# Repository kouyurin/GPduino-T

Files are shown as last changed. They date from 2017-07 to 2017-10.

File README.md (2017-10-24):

GPduino-T
=========
## 概要
GPduino-Tは、ESP32搭載のWiFiラジコン戦車制御ボードです。

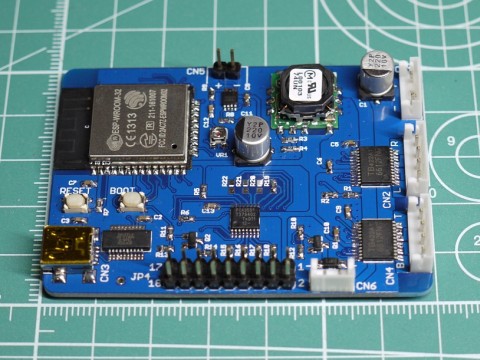
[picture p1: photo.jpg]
写真


以下のことができます。

* DCモータ4個を制御 (最大連続1.2A / 最大瞬間3.0A)
* LED 8個を制御
* サウンド出力
* 赤外線信号(38kHz変調)の送受信
* 電源 3.6V～7.2V (4.8～6V推奨)、電源電圧を監視
* WiFiによる通信　(APにもSTAにもなれる)

また、Waltersons製 1/24 バトルタンクシリーズ互換のIRバトルが可能なファームウェアを提供します。

## ファイル一覧

* hard/GPduino-T/
	* GPduino-T.sch/brd: 回路/基板設計データ(Eagle形式)
	* GPduino-T.pdf: 回路図(PDF)
	* GPduino-T_BOM.xlsx: BOMリスト(Excel形式)
	* GPduino-T.GBL/GBO/GBP/GBS/GML/GTL/GTO/GTP/GTS/TXT: ガーバデータ
* firm/GPduinoT/
	* GPduinoT.ino: ラジコン戦車のArduinoスケッチ
	* *.h, *.cpp: ラジコン戦車のための各種クラス宣言と実装 
* data/
	* cannon.bin: 砲撃音のサウンドデータ
* LICENSE: Apache Licence 2.0です。
	* ただし、回路/基板設計は、Creative Commons Attribution Share-Alike 3.0です。
* README.md これ

## Arduino開発環境のセットアップ
GPduino-T はESP32を搭載しており、Arduino IDEでファームウェアを開発できます。

ここでは、Windows10での開発環境のセットアップについて説明します。他のプラットフォームでも同様です。適宜読み替えてください。

* まず、ArduinoIDE をインストールしておきます。 (ここでは 1.8.2 を使用)
* 残念ながら、Arduino Core for the ESP32はArduino IDEのボードマネージャには対応しておらず、以下のように手作業でインストールする必要があります。
* まず、以下のリポジトリからクローンします。もしもGitが使えない場合、こちらからDownload ZIPして解凍してもかまいません。アップデートの時の手間だけの問題かと思います。
	* ソース: https://github.com/espressif/arduino-esp32.git
    * 保存先: C:/Users/ユーザ名/Documents/Arduino/hardware/espressif/esp32
* 次に、下記のバイナリを実行します。
	* C:/Users/ユーザ名/Documents/Arduino/hardware/espressif/esp32/tools/get.exe
* DOS窓が開いてインストールが実行されます。あとはDOS窓が閉じるまで待ちます。
* ノートン先生をはじめ一部のセキュリティソフトは、いくつかのバイナリをウィルスとして検出してしまうようです。(ノートン先生ではTrojan.Gen.8!cloudとして検出されます。)
* Arduino IDEの[ツール] > [マイコンボード]で[ESP32 Dev Module]を選択します。
* [ツール] > [Upload Speed]で[115200]を選択します。

## Arduinoスケッチ (Waltersonsバトルタンク互換)

Waltersons製 1/24 バトルタンクシリーズ互換の赤外線バトルが可能な以下のファームウェアを提供しています。
* firm/GPduinoT/
	* GPduinoT.ino: ラジコン戦車のArduinoスケッチ
	* *.h, *.cpp: ラジコン戦車のための各種クラス宣言と実装

Waltersonsのバトルタンクの制御基板と置き換える場合には、[こちら](http://d.hatena.ne.jp/licheng/20170421/p1)の結線表を参照してください。

## Arduinoスケッチ (ユーザー独自)
ユーザーが独自にファームウェアを作成する場合は、上記のスケッチを参考にしてください。

ラジコン戦車のための各種クラスを利用するためには、Wire.h と GPduinoR.h をインクルードします。
``` c
#include <Wire.h>
#include "GPduinoR.h"
```
すると、以下のクラスが使用できます。詳細はソースを参照してください。

* Battery: バッテリー電圧の取得
* DcMotor: DCモータの制御
* IR: 赤外線信号の送受信
* Led: LEDの制御
* Solenoid: ソレノイドの制御
* Sound: サウンドの出力
* UdpComm: WiFiによるUDP/IP通信

## Arduinoスケッチの書き込み
* GPduino-TをUSBケーブルでPCに接続します。
* 書き込み時もUSBからの給電は受けません。CN1から給電してください。
* Windows 7以降であればドライバが自動でインストールされ、COMポートとして認識されます。
	* 自動でデバイスが認識されない環境ではFTDIのデバイスドライバをインストールしてください。
* [ツール] > [シリアルポート]でESP32のポートを選択する。
* BOOTボタン(SW2)を押し下げた状態で、RESETボタン(SW1)を押して離します。これで書き込みモードになります。
* Uploadボタンで、ファームウェアを書き込みます。

## サウンドデータの書き込み
Arduinoスケッチとは別にサウンドデータもESP32のフラッシュメモリに書き込みます。

GPduinoT.ino は、フラッシュメモリの0x100000番地から61440バイトの領域に砲撃音のサウンドデータ (data/cannon.bin) が格納されているものとしています。

書き込みツール esptool.exe のあるディレクトリにパスを通しておきます。Windows10なら通常は下記ディレクトリになります。
```
C:\Users\ユーザ名\Documents\Arduino\hardware\espressif\esp32\tools
```
ESP32のBOOTボタン(SW2)を押し下げた状態で、RESETボタン(SW1)を押して離して書き込みモードにします。シリアルポートをPCに接続し、PCでCOMポート番号を確認します。ここではCOM3であったとします。そこで下記のコマンドを実行します。

```
esptool.exe -c esp32 -p COM3 -b 115200 write_flash 0x100000 cannon.bin
```

このサウンドデータは、下記のフォーマットのWAV形式ファイルから、先頭44バイトのヘッダを削除し、さらに符号なし16ビット値形式に変換するために各サンプル値に+0x8000したものです。
* サンプリング周波数 11.025kHz
* 符号つき16ビット量子化
* モノラル

## 既知の問題点

* ~~7.2V電源使用時に発熱が大きい。(3端子レギュレータをDCDCコンバータに置き換えるべき)~~ → rev.2で対応
* ~~サウンドのボリューム調整のためのトリマを追加すべき。~~ → rev.2で対応
* サウンド再生時にCPUがクラッシュする場合があるため、クラッシュ回避のごまかし処理を入れている。
* 無音時にアンプからプツプツ音が出る。
* ブリッジしやすいバターン要修正。 (SOP部品)
* D級アンプのランドパターンが短く、ハンダづけしづらい。

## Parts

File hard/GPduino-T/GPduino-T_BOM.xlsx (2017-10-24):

Gpduino-T BOM
No | Reference | Part Number | Vender | Description | DNP | Qty | Unit Price | Price | Lot Size | Supplier | Supplier Code
1 | C1,4 | 220u10V | NICHICON | チップアルミ電解コンデンサ ニチコンWT |  | 2 | 10 | 20 | 1 | 秋月 | P-10419
2 | C2,3,5-10,13 | 0.1u(1608) | (generic) | 1608型 |  | 9 | 0.325 | 2.925 | 4000 | 秋月 | P-01299
3 | C11,12 | 10nF(1608) | (generic) | 1608型 |  | 2 | 1 | 2 | 100 | 秋月 | P-04660
4 | CN1 | B3B-EH | JST | EH 3極 I型ポスト | DNP | 0 | 21 | 0 | 1 | 共立 | -
5 | CN2 | MUSB-5B-NE-S175 | Useconn Electronics | USBコネクタ Mini B メス |  | 1 | 50 | 50 | 2 | 秋月 | C-05843
6 | CN3,4 | B4B-EH | JST | EH 4極 I型ポスト | DNP | 0 | 21 | 0 | 1 | 共立 | -
7 | CN5,6 | B2B-EH | JST | EH 2極 I型ポスト | DNP | 0 | 16 | 0 | 1 | 共立 | -
8 | CN7 | - | (generic) | 2.54mmピッチ 9ピン×2列 L字ピンヘッダ | DNP | 0 | 77 | 0 | 4 | 共立 | -
9 | D1 | SS2040FL | PANJIT | ショットキーバリアダイオード 40V2A |  | 1 | 15 | 15 | 20 | 秋月 | I-02073
10 | Q1,2 | IRLML8244 | International Rectifier | Nch MOSFET (SOT23パッケージ) |  | 1 | 13 | 13 | 10 | 秋月 | I-06051
11 | R1 | 20k(1608) | (generic) | 1608型 |  | 1 | 0.2 | 0.2 | 2500 | 秋月 | R-06203
12 | R2,5-7,12,13 | 10k(1608) | (generic) | 1608型 |  | 6 | 0.2 | 1.2 | 2500 | 秋月 | R-06103
13 | R3 | 1.5k(1608) | (generic) | 1608型、±0.1% |  | 1 | 57.6 | 57.6 | 5 | RS | 566-872
14 | R4 | 680(1608) | (generic) | 1608型、±0.1% |  | 1 | 57.6 | 57.6 | 5 | RS | 566-361
15 | R8,9 | 150(1608) | (generic) | 1608型 |  | 2 | 0.2 | 0.4 | 2500 | 秋月 | R-06151
16 | R10,11,14-19 | 100(1608) | (generic) | 1608型 |  | 8 | 0.2 | 1.6 | 2500 | 秋月 | R-06101
17 | R20-22 | 100(1608) | (generic) | 1608型 | DNP | 0 | 0.2 | 0 | 2500 | 秋月 | R-06101
18 | SW1,2 | SKRPACE010 | ALPS | 表面実装タクトスイッチ |  | 2 | 20 | 40 | 5 | 秋月 | P-06185
19 | U1 | OKL-T/3-W12N | Murata | DCDCコンバータ |  | 1 | 400 | 400 | 1 | 秋月 | M-06206
20 | U2,5 | TB6621FNG | Toshiba | Dual DCモータドライバ |  | 2 | 306 | 612 | 1 | RS | 770-3797
21 | U3 | FT231XS | FTDI | USBシリアル変換 |  | 1 | 210 | 210 | 1 | 秋月 | I-06713
22 | U4 | ESP-WROOM-32 | Espressif Systems | ESP32 WiFiマイコン |  | 1 | 700 | 700 | 1 | 秋月 | M-11647
23 | U6 | PAM8303 CBSC | DiodesZetex | オーディオD級アンプ |  | 1 | 32.6 | 32.6 | 10 | RS | 790-2966
24 | U7 | PCA9551 PW | NXP | 8チャンネルLEDドライバ |  | 1 | 111 | 111 | 5 | RS | 510-730
25 | VR1 | EVM3YSX50B14 | Panasonic | 半固定抵抗器 10kΩ, 0.15W |  | 1 | 54.2 | 54.2 | 5 | RS | 731-2883
26 | - | - | Elecrow | 基板 |  | 1 | 275.1 | 275.1 | 10 | Elecrow | -
 |  |  |  |  |  |  | Total | 2656.425

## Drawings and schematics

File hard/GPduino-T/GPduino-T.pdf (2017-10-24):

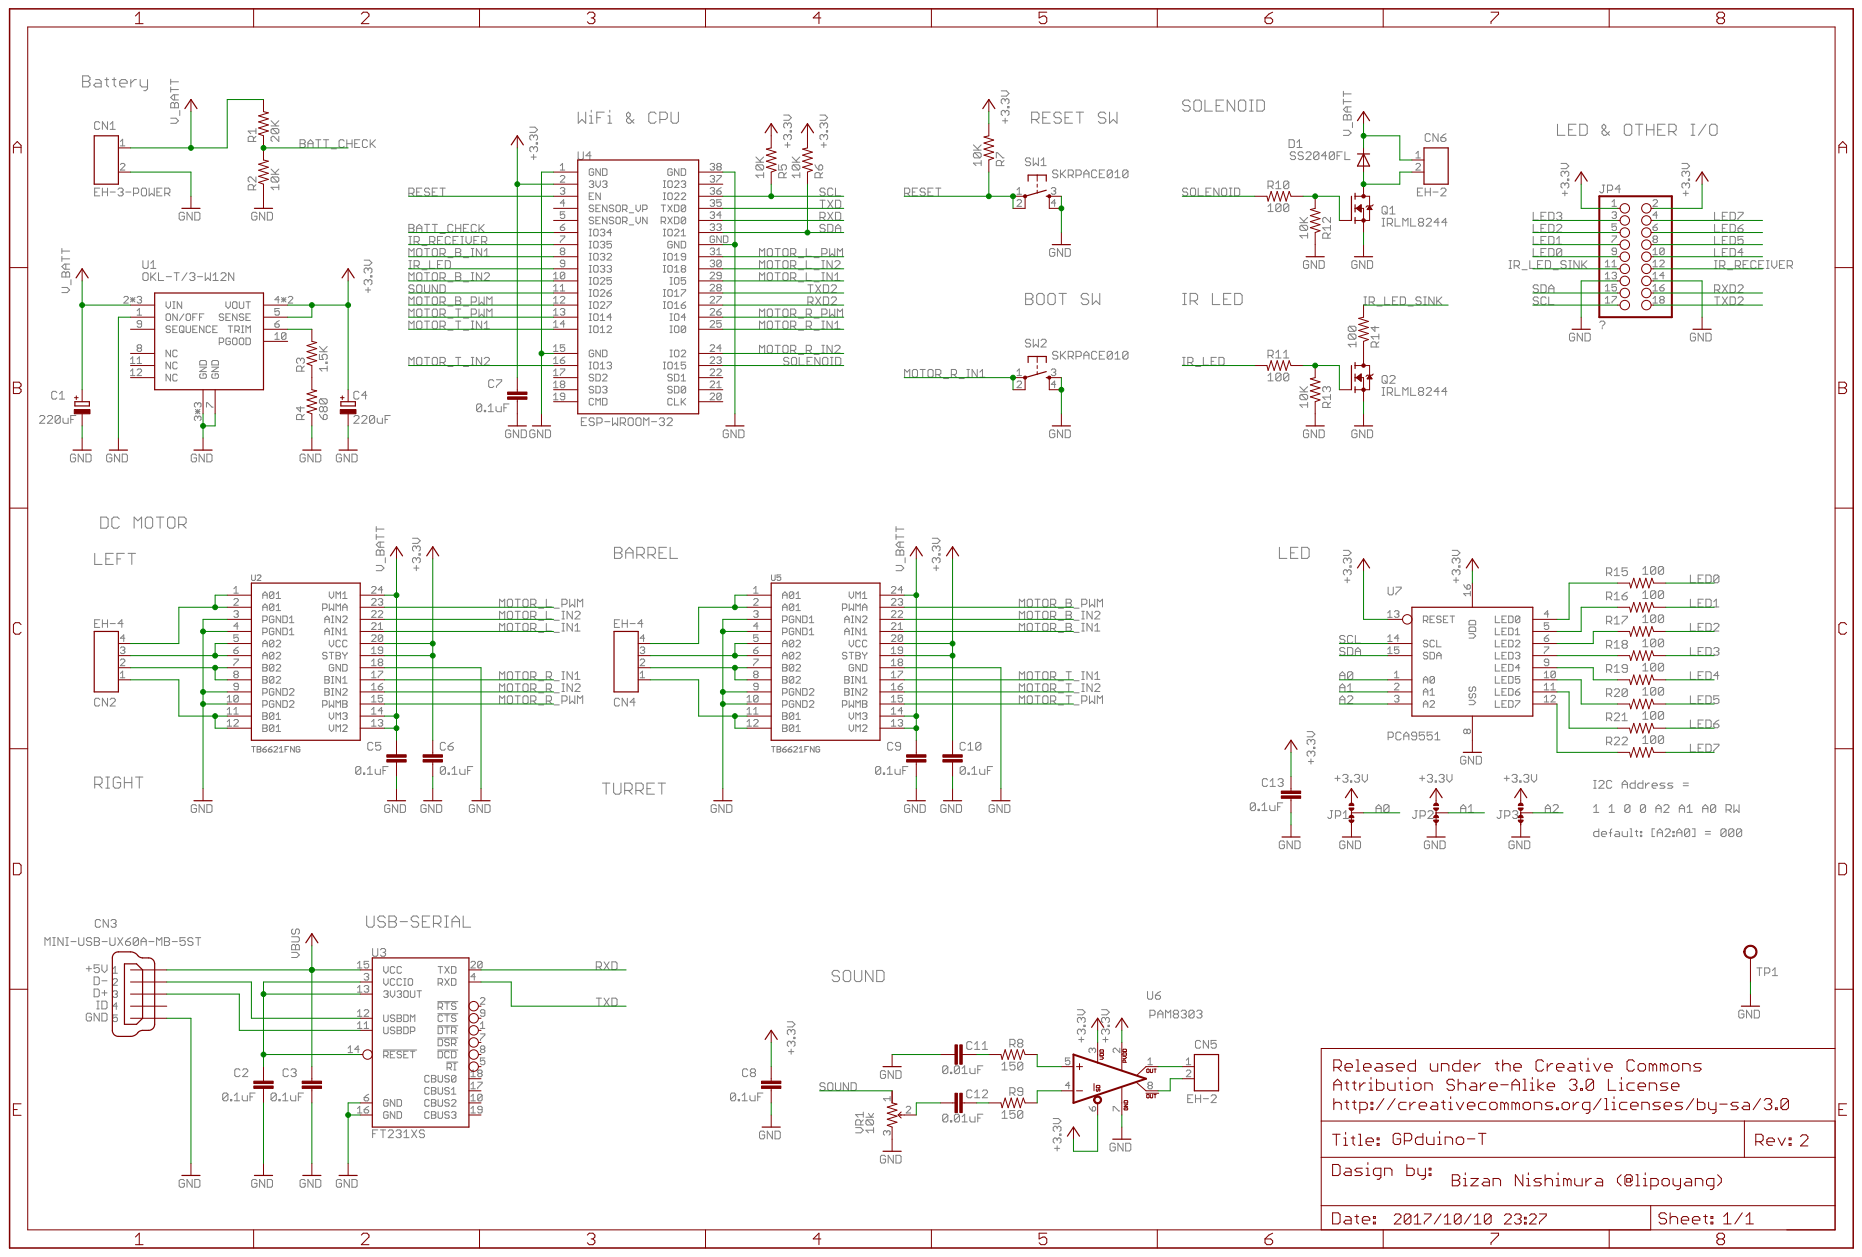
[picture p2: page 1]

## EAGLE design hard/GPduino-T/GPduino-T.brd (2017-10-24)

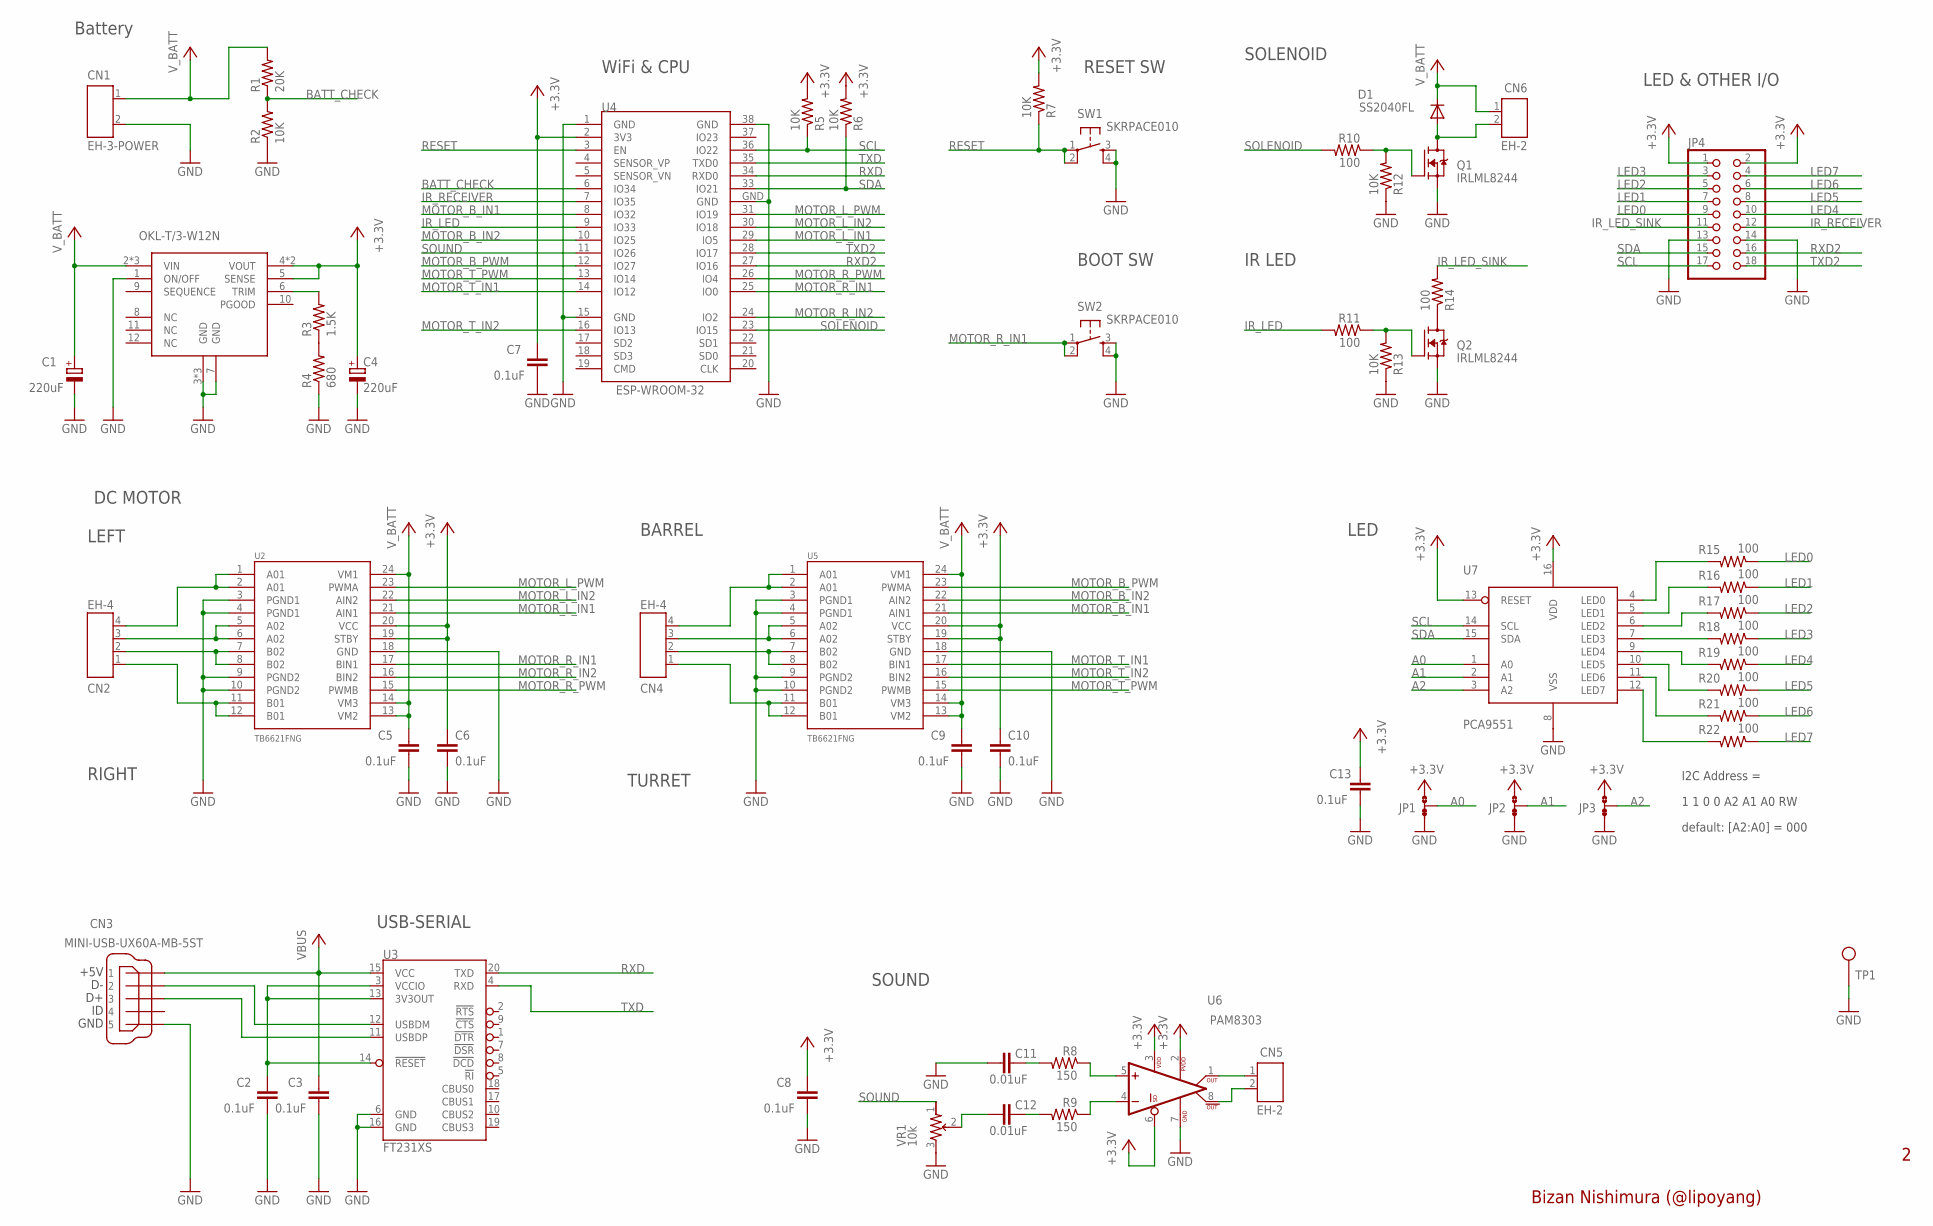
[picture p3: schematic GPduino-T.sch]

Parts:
C1, C4: 220uF; UD-6,3X7,7_NICHICON
C2, C3, C5, C6, C7, C8, C9, C10, C13: 0.1uF; C1608
C11, C12: 0.01uF; C1608
CN1: EH-3-POWER
CN2, CN4: EH-4
CN3: MINI-USB-UX60A-MB-5ST; UX60A-MB-5ST
CN5, CN6: EH-2
D1: SS2040FL; SOD123
JP1, JP2, JP3: JUMP-SHORTB; JUMP-SHORT
JP4: 2X09
Q1, Q2: IRLML8244; SOT23
R1: 20K; 0603-RES
R2, R5, R6, R7, R12, R13: 10K; 0603-RES
R3: 1.5K; 0603-RES
R4: 680; 0603-RES
R8, R9: 150; 0603-RES
R10, R11, R14, R15, R16, R17, R18, R19, R20, R21, R22: 100; 0603-RES
SW1, SW2: SKRPACE010
TP1: TEST_PIN
U1: OKL-T/3-W12N; OKL-T/X-WXXN
U2, U5: TB6621FNG; SSOP24
U3: FT231XS; SSOP20
U4: ESP-WROOM-32
U6: PAM8303; MSOP8
U7: PCA9551; TSSOP16
VR1: 10k; EVM3Y

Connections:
+3V3: C4.+, C6.1, C7.1, C8.1, C10.1, C13.1, JP1.1, JP2.1, JP3.1, JP4.1, JP4.2, R5.2, R6.2, R7.2, U1.4 (VOUT), U1.4@1 (VOUT), U1.5 (SENSE), U2.19 (STBY), U2.20 (VCC), U4.2 (3V3), U5.19 (STBY), U5.20 (VCC), U6.2 (PVDD), U6.3 (VDD), U6.6 (SD), U7.13 (RESET), U7.16 (VDD)
A0: JP1.2, U7.1 (A0)
A01: CN2.4, U2.1 (A01), U2.2 (A01)
A1: JP2.2, U7.2 (A1)
A02: CN2.3, U2.5 (A02), U2.6 (A02)
A2: JP3.2, U7.3 (A2)
A06: CN4.4, U5.1 (A01), U5.2 (A01)
A07: CN4.3, U5.5 (A02), U5.6 (A02)
BATT_CHECK: R1.1, R2.2, U4.6 (IO34)
GND: C1.-, C2.2, C3.2, C4.-, C5.2, C6.2, C7.2, C8.2, C9.2, C10.2, C11.2, C13.2, CN1.2, CN3.5, JP1.3, JP2.3, JP3.3, JP4.13, JP4.14, Q1.2 (S), Q2.2 (S), R2.1, R4.1, R12.1, R13.1, SW1.3, SW1.4, SW2.3, SW2.4, TP1.1, U1.1 (ON/OFF), U1.3 (GND), U1.3@2 (GND), U1.3@3 (GND), U1.7 (GND), U2.3 (PGND1), U2.4 (PGND1), U2.9 (PGND2), U2.10 (PGND2), U2.18 (GND), U3.6 (GND), U3.16 (GND), U4.1 (GND), U4.15 (GND), U4.38 (GND), U4.GND, U5.3 (PGND1), U5.4 (PGND1), U5.9 (PGND2), U5.10 (PGND2), U5.18 (GND), U6.7 (GND), U7.8 (VSS), VR1.3 (A)
IR_LED: R11.2, U4.9 (IO33)
IR_LED_SINK: JP4.11, R14.2
IR_RECEIVER: JP4.12, U4.7 (IO35)
LED0: JP4.9, R15.1
LED1: JP4.7, R16.1
LED2: JP4.5, R17.1
LED3: JP4.3, R18.1
LED4: JP4.10, R19.1
LED5: JP4.8, R20.1
LED6: JP4.6, R21.1
LED7: JP4.4, R22.1
MOTOR_B_IN1: U4.8 (IO32), U5.21 (AIN1)
MOTOR_B_IN2: U4.10 (IO25), U5.22 (AIN2)
MOTOR_B_PWM: U4.12 (IO27), U5.23 (PWMA)
MOTOR_L_IN1: U2.21 (AIN1), U4.29 (IO5)
MOTOR_L_IN2: U2.22 (AIN2), U4.30 (IO18)
MOTOR_L_PWM: U2.23 (PWMA), U4.31 (IO19)
MOTOR_R_IN1: SW2.1, SW2.2, U2.17 (BIN1), U4.25 (IO0)
MOTOR_R_IN2: U2.16 (BIN2), U4.24 (IO2)
MOTOR_R_PWM: U2.15 (PWMB), U4.26 (IO4)
MOTOR_T_IN1: U4.14 (IO12), U5.17 (BIN1)
MOTOR_T_IN2: U4.16 (IO13), U5.16 (BIN2)
MOTOR_T_PWM: U4.13 (IO14), U5.15 (PWMB)
unnamed: CN6.2, D1.A, Q1.3 (D)
unnamed: CN4.1, U5.11 (B01), U5.12 (B01)
unnamed: Q1.1 (G), R10.1, R12.2
unnamed: CN4.2, U5.7 (B02), U5.8 (B02)
unnamed: CN2.1, U2.11 (B01), U2.12 (B01)
unnamed: CN2.2, U2.7 (B02), U2.8 (B02)
unnamed: Q2.1 (G), R11.1, R13.2
unnamed: Q2.3 (D), R14.1
unnamed: R22.2, U7.12 (LED7)
unnamed: CN3.2, U3.12 (USBDM)
unnamed: CN3.3, U3.11 (USBDP)
unnamed: C2.1, U3.3 (VCCIO), U3.13 (3V3OUT), U3.14 (!RESET)
unnamed: R21.2, U7.11 (LED6)
unnamed: R20.2, U7.10 (LED5)
unnamed: R19.2, U7.9 (LED4)
unnamed: R18.2, U7.7 (LED3)
unnamed: R17.2, U7.6 (LED2)
unnamed: R16.2, U7.5 (LED1)
unnamed: R15.2, U7.4 (LED0)
unnamed: R8.1, U6.5 (IN+)
unnamed: R9.1, U6.4 (IN-)
unnamed: CN5.1, U6.1 (OUT+)
unnamed: C11.1, R8.2
unnamed: C12.1, R9.2
unnamed: CN5.2, U6.8 (OUT-)
unnamed: C12.2, VR1.2 (S)
unnamed: R3.1, R4.2
unnamed: R3.2, U1.6 (TRIM)
RESET: R7.1, SW1.1, SW1.2, U4.3 (EN)
RXD: U3.20 (TXD), U4.34 (RXD0)
RXD2: JP4.16, U4.27 (IO16)
SCL: JP4.17, R5.1, U4.36 (IO22), U7.14 (SCL)
SDA: JP4.15, R6.1, U4.33 (IO21), U7.15 (SDA)
SOLENOID: R10.2, U4.23 (IO15)
SOUND: U4.11 (IO26), VR1.1 (E)
TXD: U3.4 (RXD), U4.35 (TXD0)
TXD2: JP4.18, U4.28 (IO17)
VBUS: C3.1, CN3.1, U3.15 (VCC)
V_BATT: C1.+, C5.1, C9.1, CN1.1, CN6.1, D1.C, R1.2, U1.2 (VIN), U1.2@2 (VIN), U1.2@3 (VIN), U2.13 (VM2), U2.14 (VM3), U2.24 (VM1), U5.13 (VM2), U5.14 (VM3), U5.24 (VM1)

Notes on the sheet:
Battery
LEFT
Bizan Nishimura (@lipoyang)
RIGHT
1 1 0 0 A2 A1 A0 RW
I2C Address =
default: [A2:A0] = 000
USB-SERIAL
DC MOTOR
WiFi & CPU
RESET SW
BOOT SW
TURRET
BARREL
SOLENOID
IR LED
LED & OTHER I/O
LED
SOUND

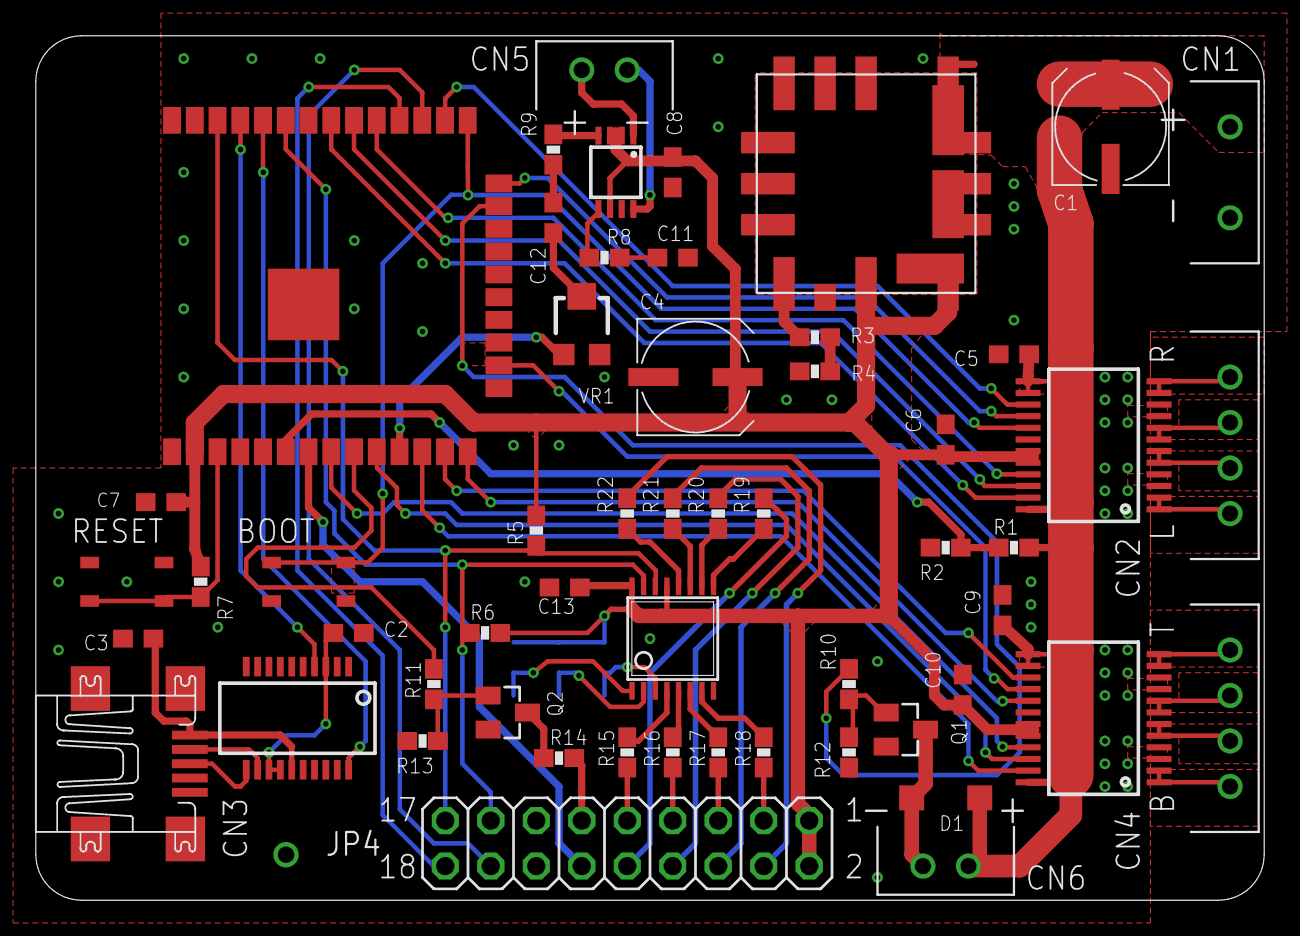
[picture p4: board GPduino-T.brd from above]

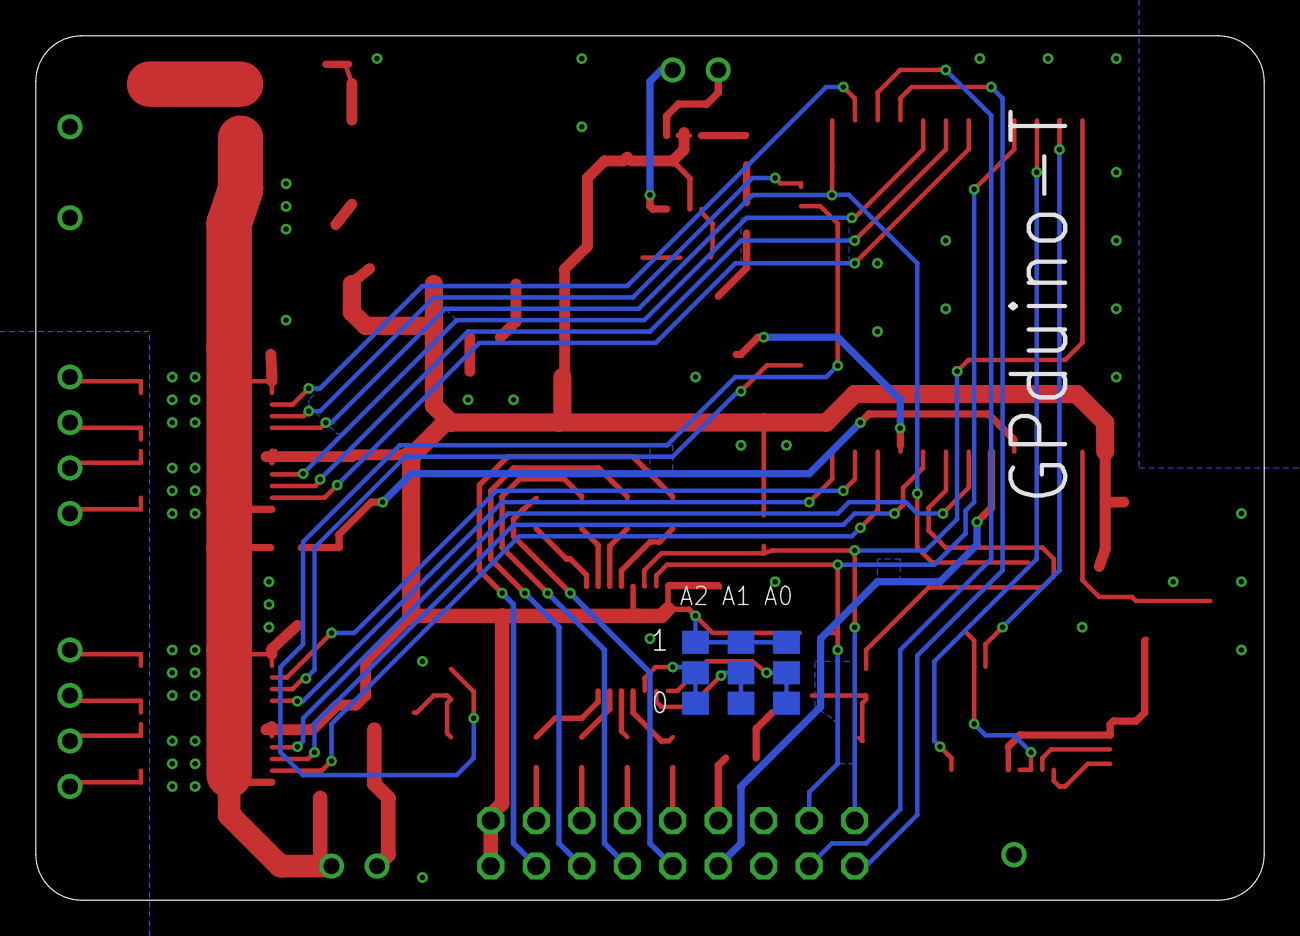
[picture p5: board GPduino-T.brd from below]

Board: 2 copper layers, 68.6 x 48.3 mm, 59 parts (3 on the bottom side), 72 nets.

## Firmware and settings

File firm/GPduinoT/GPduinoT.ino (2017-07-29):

#include <Wire.h>
#include "GPduinoT.h"

// UDP
UdpComm udpComm;

// State
#define STATE_RUNNING   0
#define STATE_SHOOT     1
#define STATE_HIT       2
#define STATE_HALT      3
int mainState;

// IR Receiver & IR LED
IR ir(PIN_IR_RECEIVER, PIN_LED_IR_GUN, PWM_LED_IR_GUN, TIMER_IR_GUN);

// LED
Led ledHeadLight  (LED_HEAD_LIGHT);
Led ledShooting   (LED_SHOOTING);
Led ledHit        (LED_HIT);
Led ledStatusRed  (LED_STATUS_RED);
Led ledStatusGreen(LED_STATUS_GREEN);

// DC Motor
DcMotor motorBarrel(
    PIN_MOTOR_BARREL_IN1, PIN_MOTOR_BARREL_IN2,
    PIN_MOTOR_BARREL_PWM, PWM_MOTOR_BARREL);
DcMotor motorTurret(
    PIN_MOTOR_TURRET_IN1, PIN_MOTOR_TURRET_IN2,
    PIN_MOTOR_TURRET_PWM, PWM_MOTOR_TURRET);
DcMotor motorLeft(
    PIN_MOTOR_LEFT_IN1, PIN_MOTOR_LEFT_IN2,
    PIN_MOTOR_LEFT_PWM, PWM_MOTOR_LEFT);
DcMotor motorRight(
    PIN_MOTOR_RIGHT_IN1, PIN_MOTOR_RIGHT_IN2,
    PIN_MOTOR_RIGHT_PWM, PWM_MOTOR_RIGHT);

// Battery checker
Battery battery(PIN_ADC_BATTERY, BATTERY_DIV_RATIO);

// Solenoid
Solenoid solenoid(PIN_SOLENOID, PWM_SOLENOID);

// Sound
Sound sound(TIMER_SOUND);

// 10msec Timer
hw_timer_t *timer10ms;
// 10msec Timer flag
bool flag10ms;

// Counter for shooting LED
int cntShootingLED;
// Counter for shooting action
int cntShootingAction;

// Counter for hit LED
int cntHitLED;
// Counter for hit action
int cntHitAction;

// Counter for loading time
int cntLoadingTime;

// Crawler control
int ctrlFB;  // Forward-Backword
int ctrlLR;  // Left-Right

// Hit Point
int hitPoint;

// Battery voltage check
void battery_check()
{
    static char txbuff[256];
    
    if(!udpComm.isReady()) return;
    
    static int cnt2 = 0;

    unsigned short Vbat_ave = battery.getAdc() >> 2;
    //Serial.print("Vbat_ave");Serial.println(Vbat_ave);

    // send battery voltage value every about 1 sec
    cnt2++;
    if(cnt2 >= 100)
    {
        cnt2=0;
        
        txbuff[0]='#';
        txbuff[1]='B';
        Uint16ToHex(&txbuff[2], Vbat_ave, 3);
        txbuff[5]='$';
        txbuff[6]='\0';
        udpComm.send(txbuff);
        Serial.print("battery_check ");
        Serial.println(Vbat_ave);
    }
}

// Crawler control
void crawler_control()
{
    int r = (int)(ctrlFB - ctrlLR)*8;
    int l = (int)(ctrlFB + ctrlLR)*8;

    motorLeft.out(l);
    motorRight.out(r);
}

// handler called when this tank is hit
void onHit(int team, int gunClass)
{
    Serial.print("onHit ");
    Serial.print(team);
    Serial.print(" ");
    Serial.println(gunClass);
    
    // Hit Point decrement
    if(hitPoint > 0) hitPoint--;
    switch(hitPoint){
    case 5:
        // Green:Blink(1s) Red:Off
        ledStatusGreen.blink(LED_BLINK_CYCLE_1S);
        ledStatusRed.turnOff();
        break;
    case 4:
        // Green:Blink(0.5s) Red:Off
        ledStatusGreen.blink(LED_BLINK_CYCLE_0_5S);
        ledStatusRed.turnOff();
        break;
    case 3:
        // Green:Off Red:On
        ledStatusGreen.turnOff();
        ledStatusRed.turnOn();
        break;
    case 2:
        // Green:Off Red:Blink(1s)
        ledStatusGreen.turnOff();
        ledStatusRed.blink(LED_BLINK_CYCLE_1S);
        break;
    case 1:
        // Green:Off Red:Blink(0.5s)
        ledStatusGreen.turnOff();
        ledStatusRed.blink(LED_BLINK_CYCLE_0_5S);
        break;
    case 0: // Crush!!
        // Green:Off Red:Off
        ledStatusGreen.turnOff();
        ledStatusRed.turnOff();
        break;
    }
    
    // LED
    if(hitPoint > 0){
        ledHit.turnOn();
        cntHitLED = TIME_HIT;
    }else{
        ledHit.blink(LED_BLINK_CYCLE_1S);
        ledHeadLight.turnOff();
    }
    
    // Hit action
    ctrlLR = ACTION_PWM;
    ctrlFB = 0;
    crawler_control();
    cntHitAction = TIME_HIT;
    cntShootingAction = 0;
    
    // TODO
    //digitalWrite(17, LOW);
    //delay(1000);
    //digitalWrite(17, HIGH);
}

// 10msec cycle timer handler
void IRAM_ATTR on10msTimer()
{
    const static DRAM_ATTR bool TRUE = true;
    flag10ms = TRUE;
}

// initialize
void setup()
{
    // Variables
    mainState = STATE_RUNNING;
    flag10ms = false;
    ctrlFB = 0;
    ctrlLR = 0;
    hitPoint = HIT_POINT_FULL;
    cntShootingLED = 0;
    cntShootingAction = 0;
    cntHitLED = 0;
    cntHitAction = 0;
    cntLoadingTime = 0;
    
    //delay(100); // This is necessary! I can't understand why
    
    // Serial
    Serial.begin(115200);
    Serial.println("setup() start!");
    
    // I2C
    Wire.begin();
    
    // UDP communication
    udpComm.beginAP(NULL, "12345678");
    udpComm.onReceive = UdpComm_callback;
    
    // Sound
    sound.begin();
    
    // IR Receiver & IR LED
    ir.setTeam(BATTLE_ROYAL);
    ir.setGun(GUN_20P);
    ir.setOnHit(onHit);
    ir.begin();
    
    // LED
    ledHeadLight.begin();
    ledShooting.begin();
    ledHit.begin();
    ledStatusRed.begin();
    ledStatusGreen.begin();
    
    ledHeadLight.turnOn();    // Head Light LED:   ON
    ledShooting.turnOff();    // Shooting LED:     OFF
    ledHit.turnOff();         // Hit LED:          OFF
    ledStatusRed.turnOff();   // Status Red LED:   OFF
    ledStatusGreen.turnOn();  // Status Green LED: ON
/*
    // TEST
    ledHeadLight.turnOn();
    ledShooting.blink(LED_BLINK_CYCLE_1S);
    ledHit.turnOn();
    ledStatusRed.turnOn();
    ledStatusGreen.blink(LED_BLINK_CYCLE_1S);
*/
    
    // DC Motor
    motorBarrel.begin();
    motorTurret.begin();
    motorLeft.begin();
    motorRight.begin();

    // Battery checker
    battery.begin();
    
    // Solenoid
    solenoid.begin();
    solenoid.out(512); // TODO
    
    // 10msec Timer
    noInterrupts();
    timer10ms = timerBegin(TIMER_10MS, TIMER_DIV_1US, true);
    timerAttachInterrupt(timer10ms, &on10msTimer, true);
    timerAlarmWrite(timer10ms, TIMER_CYCLE_10MS, true);
    timerStart(timer10ms);
    timerAlarmEnable(timer10ms);
    interrupts();
    
    // TEST TODO
    pinMode(16, INPUT_PULLUP);
    pinMode(17, OUTPUT);
    digitalWrite(17, HIGH);
    
    Serial.println("setup() end!");
}

int io0_last = HIGH;

// main loop
void loop()
{
    static int cnt = 0;

    // UDP communication
    udpComm.loop();
    
    // IR receive
    ir.loop();
    
    // Sound data load
    sound.loop();
    
    // TODO (for test)
    int io0 = digitalRead(16);
    if((io0 == LOW) && (io0_last == HIGH)){
        // IR shoot
        ir.shoot(2);
        // Shooting LED
        ledShooting.turnOn();
        // Recoil action
        ctrlLR = 0;
        ctrlFB = -ACTION_PWM;
        crawler_control();
        // time counter
        cntShootingAction = TIME_SHOOTING;
        cntShootingLED = TIME_SHOOTING;
        cntLoadingTime = TIME_LOADING;
        cntHitAction = 0;
        delay(50);
        sound.play(SOUND_SEG_CANNON, SOUND_SIZE_CANNON);
    }
    io0_last = io0;
    
    // 10msec timer
    if(flag10ms){
        flag10ms = false;
        
        // battery check
        battery_check();
        
        // Hit action time
        if(cntHitAction > 0){
            cntHitAction--;
            if(cntHitAction == TIME_ACTION*3){
                ctrlLR = -ACTION_PWM;
                ctrlFB = 0;
                crawler_control();
            }
            else if(cntHitAction == TIME_ACTION*2){
                ctrlLR = ACTION_PWM;
                ctrlFB = 0;
                crawler_control();
            }
            else if(cntHitAction == TIME_ACTION*1){
                ctrlLR = -ACTION_PWM;
                ctrlFB = 0;
                crawler_control();
            }
            else if(cntHitAction <= 0){
                ctrlLR = 0;
                ctrlFB = 0;
                crawler_control();
            }
        }
        // Hit LED lighting time
        if(cntHitLED > 0){
            cntHitLED--;
            if(cntHitLED <= 0){
                ledHit.turnOff();
            }
        }
        // Shooting action time
        if(cntShootingAction > 0){
            cntShootingAction--;
            if(cntShootingAction == TIME_ACTION){
                ctrlLR = 0;
                ctrlFB = ACTION_PWM;
                crawler_control();
            }
            else if(cntShootingAction <= 0){
                ctrlLR = 0;
                ctrlFB = 0;
                crawler_control();
            }
        }
        // Shooting LED lighting time
        if(cntShootingLED > 0){
            cntShootingLED--;
            if(cntShootingLED <= 0){
                ledShooting.turnOff();
            }
        }
        // Canon loading time
        if(cntLoadingTime > 0){
            cntLoadingTime--;
        }
    }

    delay(1);
}

// UDP command received callback
// buff: command string buffer
void UdpComm_callback(char* buff)
{
    unsigned short val;
    int sval, sval2;
    int deg;
    int ch;
    int i;
    
    //Serial.print("udpComm_callback:");Serial.println(buff);
    
    if(buff[0] != '#') return;
    buff++;

    // TODO
    //if(hitPoint == 0) return; // No hit point is left
    
    switch(buff[0])
    {
    /* D-Command (Crawler Drive Forward/Backward)
       format: #Dxx$
       xx: 0->Stop, Positive->Forward, Negative->Backward
     */
    case 'D':
        // When shooting or hit, D-Command is invalid
        if( cntShootingAction > 0 ) break;
        if( cntHitAction > 0 ) break;
        
        if( HexToUint16(&buff[1], &val, 2) != 0 ) break;
        sval = (int)((signed char)val);
        
        ctrlFB = sval;
        crawler_control();
        break;
        
    /* T-Command (Crawler Turn Right/Left)
       format: #Txxn$
       n: ignored (this parameter is for racing car controller)
       xx: 0->Neutral, Positive->Right, Negative->Left
     */
    case 'T':
        // When shooting or hit, T-Command is invalid
        if( cntShootingAction > 0 ) break;
        if( cntHitAction > 0 ) break;
        
        if( HexToUint16(&buff[1], &val, 2) != 0 ) break;
        sval = (int)((signed char)val);
        
        ctrlLR = sval;
        crawler_control();
        break;
        
    /* G-Command (Barrel Up/Down)
     */
    case 'G':
        if( HexToUint16(&buff[1], &val, 2) != 0 ) break;
        sval = (int)((signed char)val);
        
        if(sval > 64){
            motorBarrel.out(512);
        }else if(sval < -64){
            motorBarrel.out(-512);
        }else{
            motorBarrel.out(0);
        }
        break;
        
    /* R-Command (Turret Turn Right/Left)
     */
    case 'R':
        if( HexToUint16(&buff[1], &val, 2) != 0 ) break;
        sval = (int)((signed char)val);
        
        if(sval > 64){
            motorTurret.out(512);
        }else if(sval < -64){
            motorTurret.out(-512);
        }else{
            motorTurret.out(0);
        }
        break;
        
    /* F-Command (Fire)
     */
    case 'F':
        if(buff[1] >= '1'){
#ifndef DEMO_MB_OSAKA // No limit for rapid-fire
            if(cntLoadingTime == 0){
#endif
                int code = (int)(buff[1] - '1');
                // IR shoot
                ir.shoot(code);
                // Shooting LED
                ledShooting.turnOn();
                // Recoil action
                ctrlLR = 0;
                ctrlFB = -ACTION_PWM;
                crawler_control();
                // time counter
                cntShootingAction = TIME_SHOOTING;
                cntShootingLED = TIME_SHOOTING;
                cntLoadingTime = TIME_LOADING;
                cntHitAction = 0;
                // sound
                sound.play(SOUND_SEG_CANNON, SOUND_SIZE_CANNON);
#ifndef DEMO_MB_OSAKA
            }
#endif
        }else if(buff[1] == '0'){
            ;
        }
        break;
    }
}

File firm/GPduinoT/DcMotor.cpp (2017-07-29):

#include <Arduino.h>

#include "DcMotor.h"

#define PWM_FREQUENCY   1000
#define PWM_RESOLUTION  10
#define PWM_MAX         1023

// constructor
// pinIn1: pin number of IN1
// pinIn2: pin number of IN2
// pinPwm: pin number of PWM
// chPwm: channel number of PWM
DcMotor::DcMotor(int pinIn1, int pinIn2, int pinPwm, int chPwm)
{
    m_pinIn1 = pinIn1;
    m_pinIn2 = pinIn2;
    m_pinPwm = pinPwm;
    m_chPwm = chPwm;
}

// begin the DC motor driver
void DcMotor::begin()
{
    // initialize PWM
    ledcAttachPin(m_pinPwm, m_chPwm);
    ledcSetup(m_chPwm, PWM_FREQUENCY, PWM_RESOLUTION);
    ledcWrite(m_chPwm, 0);
    
    // initialize GPIO
    digitalWrite(m_pinIn1, LOW);
    digitalWrite(m_pinIn2, LOW);
    pinMode(m_pinIn1, OUTPUT);
    pinMode(m_pinIn2, OUTPUT);
}

// drive the motor
// value: output value (-1023 to +1023)
void DcMotor::out(int value)
{
    int pwm = abs(value);
    if(pwm<0) pwm = 0;
    if(pwm>PWM_MAX) pwm = PWM_MAX;
    
    int in1,in2;
    if(value > 0){
        in1 = LOW;
        in2 = HIGH;
    }else if(value < 0){
        in1 = HIGH;
        in2 = LOW;
    }else{
        in1 = LOW;
        in2 = LOW;
        pwm = 0;
    }

    digitalWrite(m_pinIn1, in1);
    digitalWrite(m_pinIn2, in2);
    ledcWrite(m_chPwm, pwm);
}

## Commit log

2017-07-29 回路設計データを追加
    [GPduino-T.GBL, GPduino-T.GBO, GPduino-T.GBP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]
2017-07-29 READMEを追加
2017-07-29 ファーウェアの追加
2017-08-02 READMEを修正
2017-08-02 砲撃サウンドデータの追加
2017-08-02 READMEの修正
2017-10-24 rev.2基板
    [GPduino-T.brd, GPduino-T.sch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]

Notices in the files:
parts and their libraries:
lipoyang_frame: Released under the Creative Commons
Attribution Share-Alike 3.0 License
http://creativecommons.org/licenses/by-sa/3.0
